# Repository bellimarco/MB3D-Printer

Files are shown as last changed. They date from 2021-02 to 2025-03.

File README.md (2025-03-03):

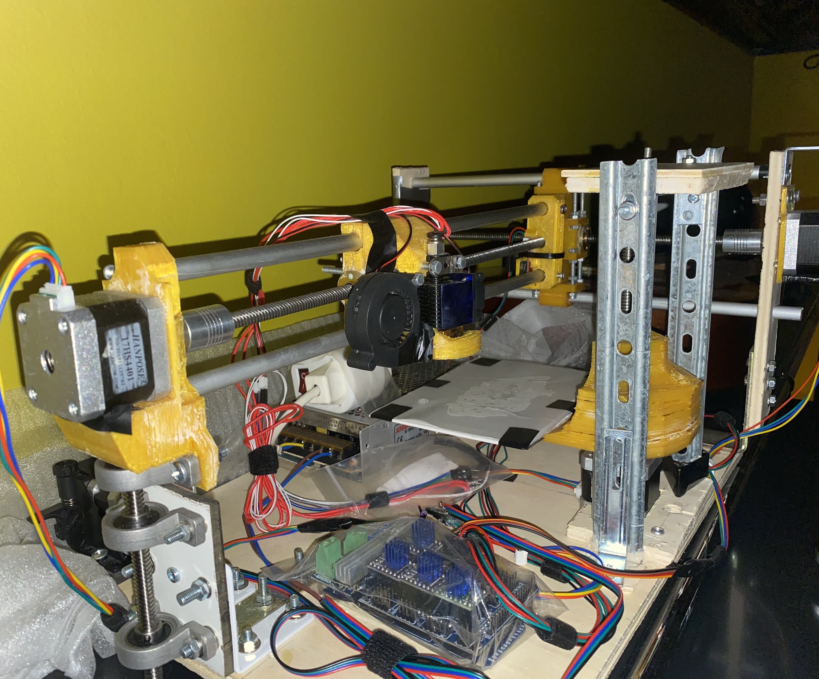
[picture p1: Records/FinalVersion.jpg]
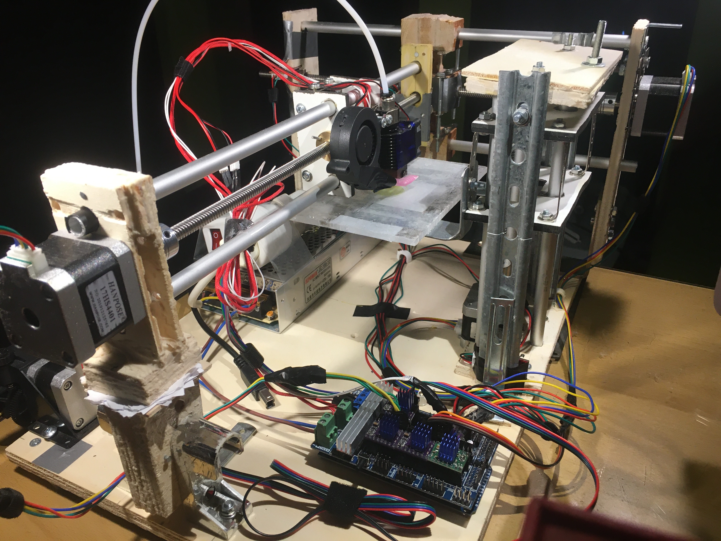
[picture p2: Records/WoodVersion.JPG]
 

The 3D Printer I built during the 2020 quarantine. Like the [plotter project](https://github.com/bellimarco/DisegnatoreRemoto) I had just finished, it is based on a polar setup with two stepper motors for radius and angle, and another stepper for the bed height.

An Arduino Mega with the RAMPS shield controls the actuators, filament extruder, end stops, heat block and thermistors; it receives Gcodes via serial from a computer. The bottleneck in printing speed was the microcontroller frequency, which wasn't enough to handle both serial communication and a smooth stepper motor control (which requires constantly sending precisely timed step signals to the four steppers). Therefore, I decided to separated these two processes: the Arduino listens on the serial port until filling a buffer of about 50 Gcodes, and then it starts executing them until the buffer is empty. The occasional waiting time (+-1 sec) for the Gcode buffer to fill up results inevitably in some artifacts on the final print due to the stillness of the printhead.

To create the Gcodes from the stl files I used the Cura software. With a NodeJS program, I translated the Cura files (meant for a classic CoreXY design) to a custom Gcode standard created to fit the model of my 3D printer. Then, I create a local server on the computer with another NodeJS program (mb3d.js) which sends via serial the Gcodes to the Arduino. The printing process can be monitored by a rudimentary user interface on a webpage connecting to the server.

In addition, the printer was built from scratch using wood and metal parts from my local carpentry shop. Only after having built a functioning wooden prototype, could I upgrade it with better 3D printed parts. I wanted to avoid building my first 3D printer with 3D printed parts obtained somewhere else because that feels a bit like cheating, doesn't it ?

## Resources
For more images and videos of the project I refer to my [Google Drive folder](https://drive.google.com/drive/folders/1L6Rk5TGIUBfg1ZFhCpQsbyhUCCYRQrp4?usp=share_link).

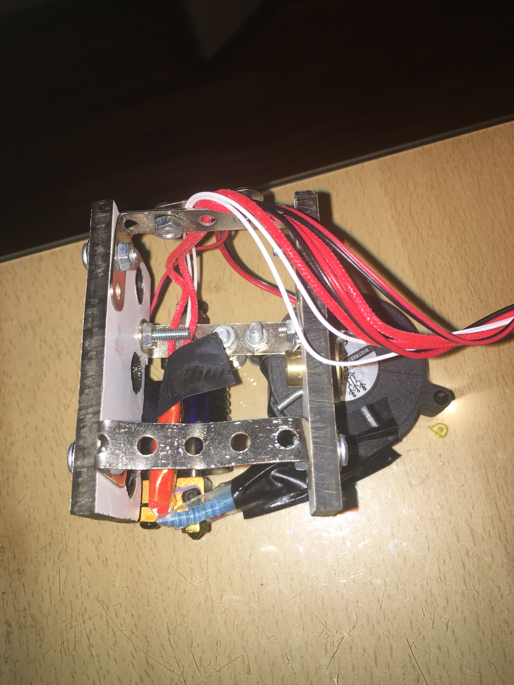
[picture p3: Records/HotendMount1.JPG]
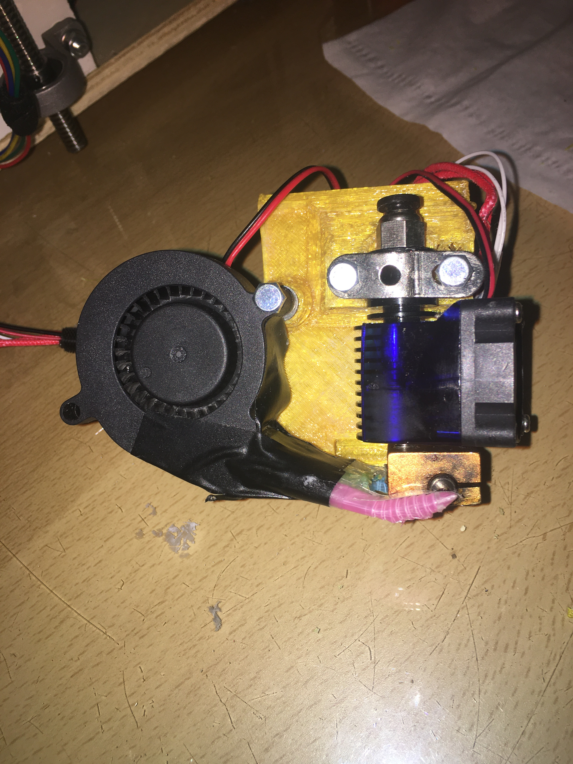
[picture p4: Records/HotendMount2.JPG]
 

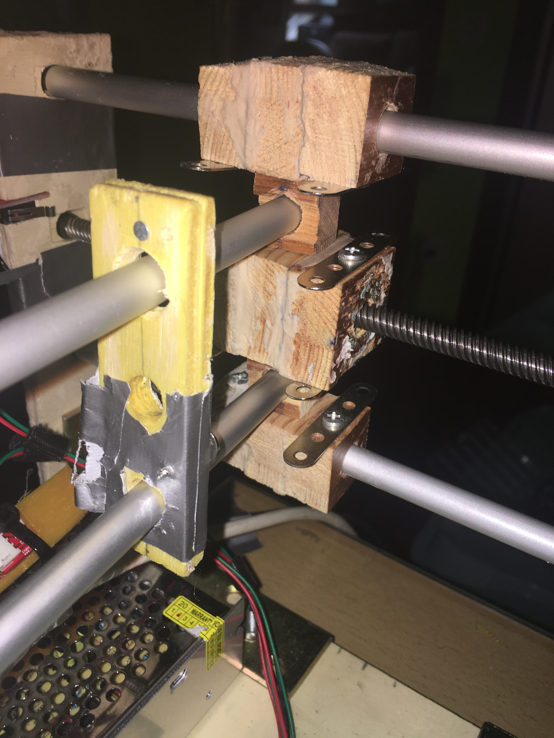
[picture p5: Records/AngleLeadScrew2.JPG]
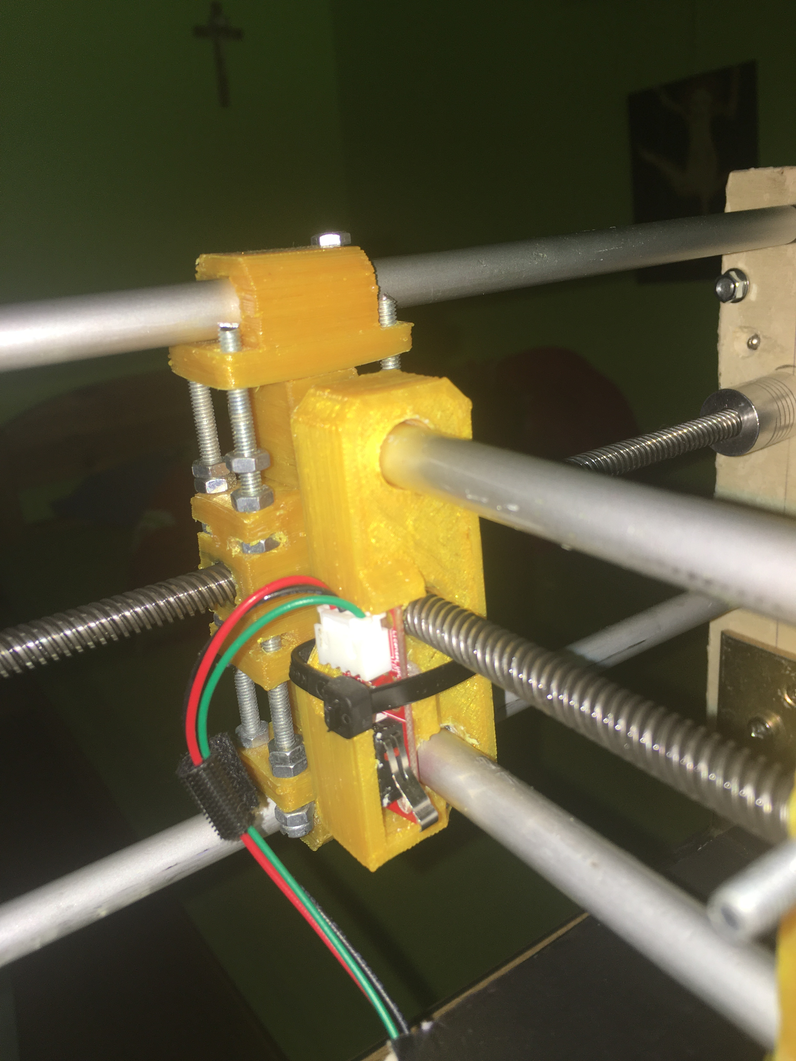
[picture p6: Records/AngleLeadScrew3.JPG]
 

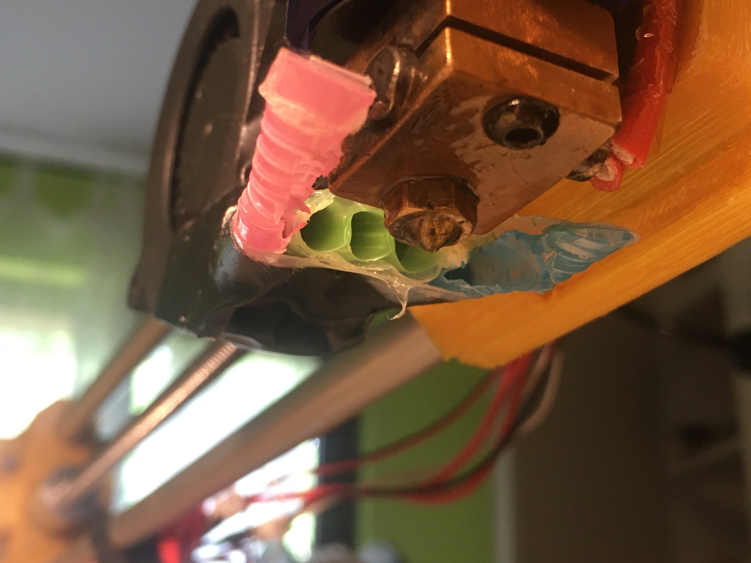
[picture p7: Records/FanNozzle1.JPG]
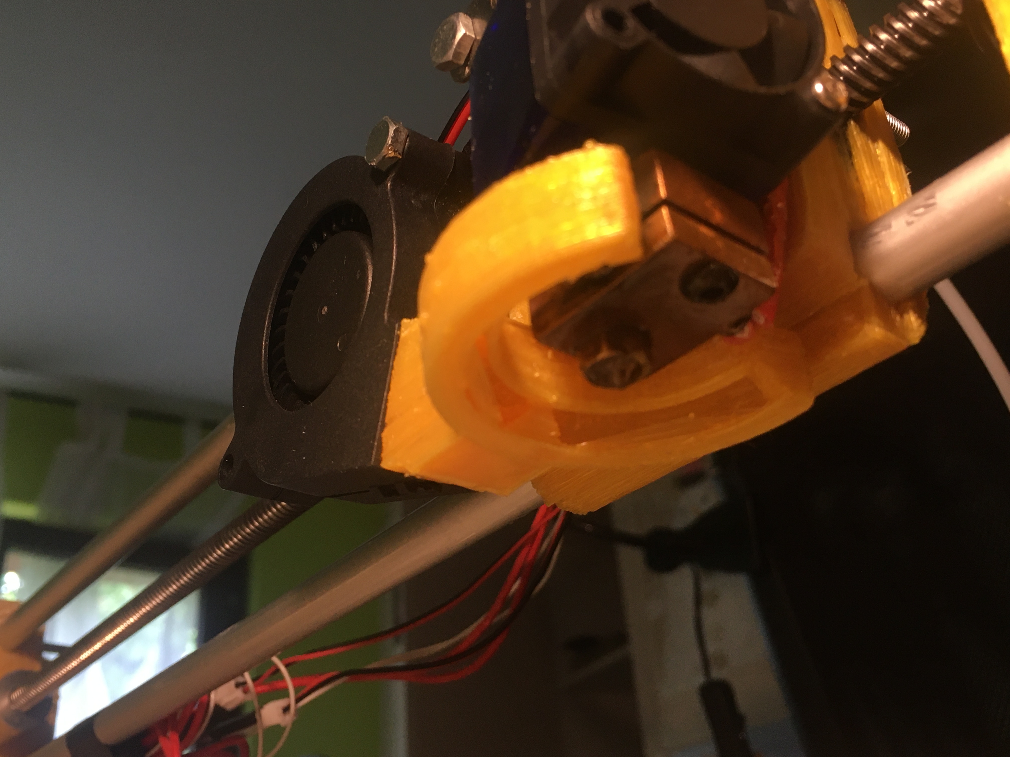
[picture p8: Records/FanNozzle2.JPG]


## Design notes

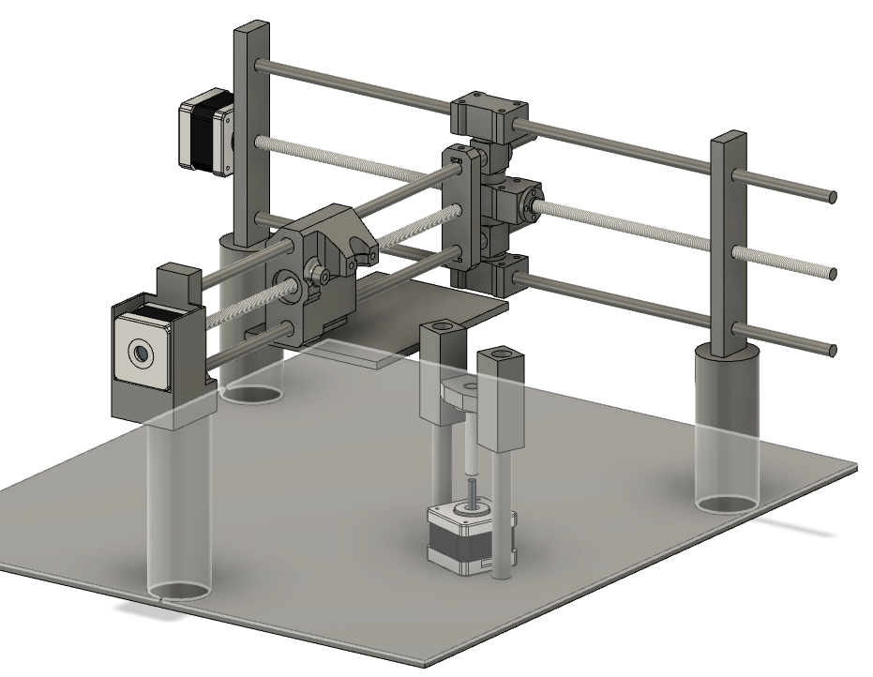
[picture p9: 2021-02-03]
Records/3dmodel.png

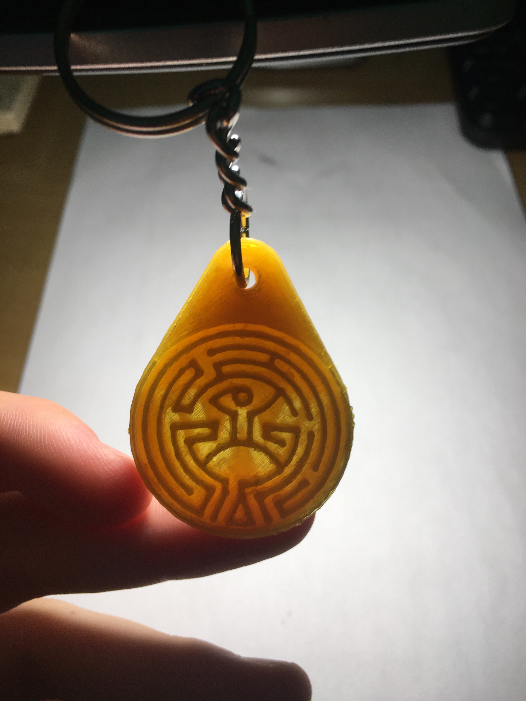
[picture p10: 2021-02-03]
Records/WestworldMaze2.JPG

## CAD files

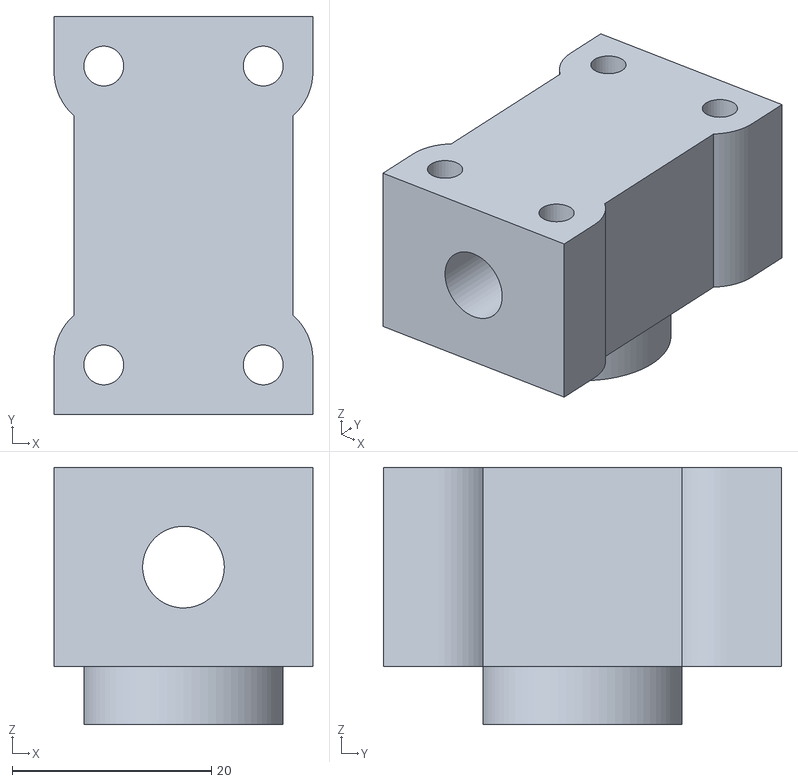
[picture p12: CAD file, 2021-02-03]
3DParts/ARailBott.stl
26.0 x 40.0 x 25.8

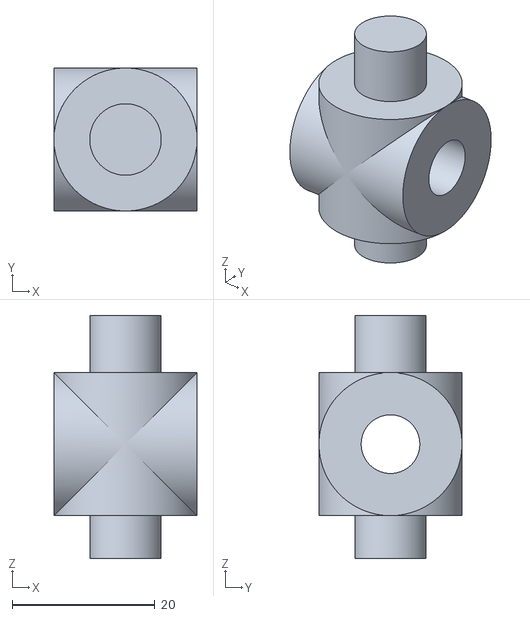
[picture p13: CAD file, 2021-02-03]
3DParts/RShaftSupportTop.stl
20.0 x 20.0 x 34.0

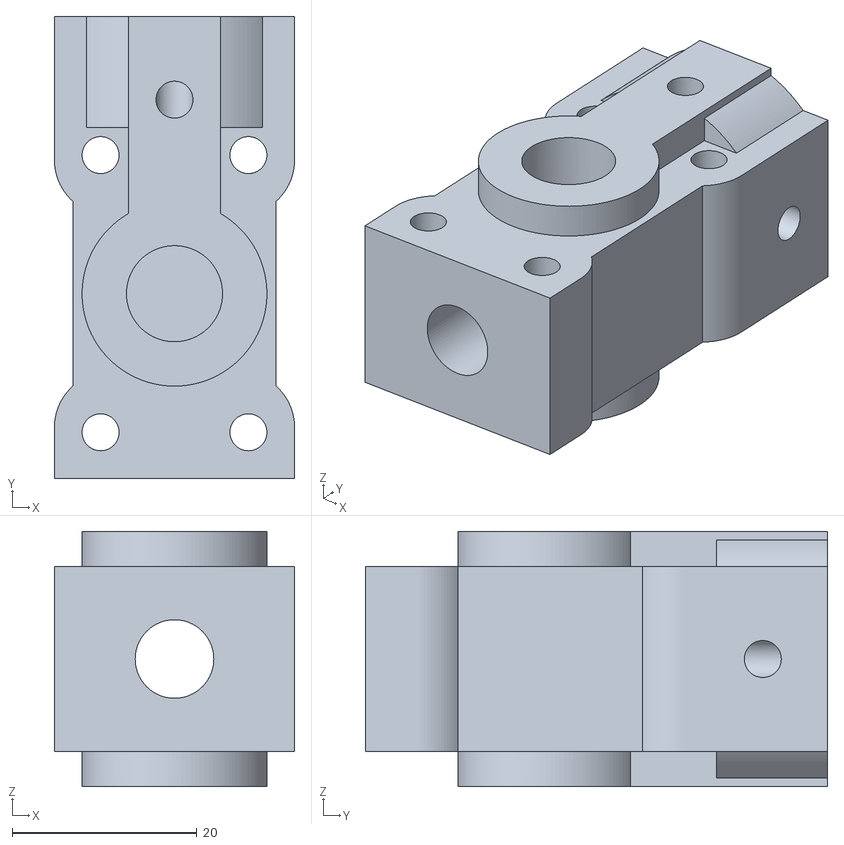
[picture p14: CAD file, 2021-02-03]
3DParts/ARailMiddle.stl
26.0 x 50.0 x 27.6

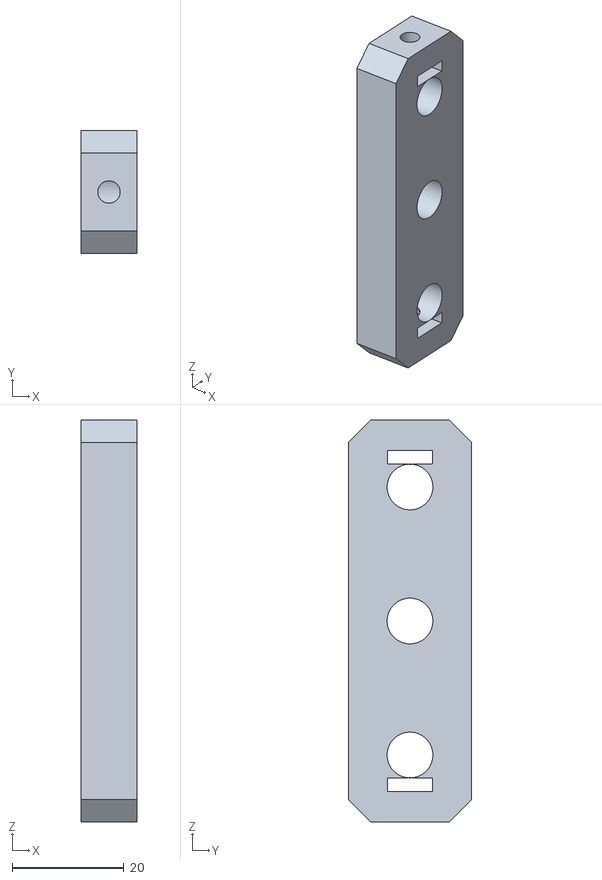
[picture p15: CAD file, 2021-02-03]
3DParts/LeadScrewRHolder.stl
10.0 x 22.0 x 72.0

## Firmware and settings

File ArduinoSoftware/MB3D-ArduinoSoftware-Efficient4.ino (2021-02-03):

#include "Pin.h"
#include "GlobalVariables.h"

#include <digitalWriteFast.h>

#include "ThermistorData.h"
#include "ThermalManagement.h"



//-----------------------------SETUP AND LOOP--------------------------

void setup() {

  Serial.begin(115200);
  SerialMsg.reserve(100);
  for(int i=0; i<BufferSize; i++){ Buffer[i]="/"; }

  SetPins();
  ResetPins();
 
}



void loop() {
  Time=millis();

  if(AutoNextCode){
    if(NextCodeTimert<Time){
      NextCodeTimert=Time+NextCodeTimerT;
      if(BufferHead!=BufferTail){
        AutoNextCode=false;
        Serial.print("autonext}");
        NextCode();
      }
    }
  }

  ThermalTimerUpdate();

  if(FinishedCode){
    CheckSerial();
    if(MotionCode && !NextPresent){
      RunMotionQueue();
    }
    FinishCode();
  }
  
  
  delay(LoopDelay);
}

//-----------------------------SETUP AND LOOP--------------------------





//---------------------COMMUNICATION ALGORITHM--------------------------

void serialEvent(){
  delay(100);
  CheckSerial();
}
void CheckSerial(){
  Time=millis();
  NextCodeTimert=Time+NextCodeTimerT;
  char c=' ';
  while(Serial.available()){
    c=Serial.read();
    if(c=='{'){
      SerialComplete=false;
      SerialMsg="";
    }else if(c=='}'){
      if(!SerialComplete){
        if(SerialMsg.equals("report")){
          PrintReport();
        }else{
          if(DepthLog){ Serial.print("echo/adding buffer: "+SerialMsg+"}"); }
          Serial.print("buf}");
          Buffer[BufferTail]=SerialMsg;
          BufferTail=(BufferTail+1==BufferSize)?0:(BufferTail+1);
        }
      }
      SerialComplete=true;
      SerialMsg="";
    }else if(!SerialComplete){
      SerialMsg+=c;
    }
  }
}

//finish the current code
void FinishCode(){
  MotionCode=false;
  FinishedCode=false;
  Serial.print("fin}");
  Buffer[BufferHead]="/";
  BufferHead=(BufferHead+1==BufferSize)?0:(BufferHead+1);
  if(BufferHead!=BufferTail){
    NextCode();
  }else{
    AutoNextCode=true;
    NextCodeTimert=0;
  }
}
//call next code in the buffer
void NextCode(){
  if(DepthLog){ Serial.print("echo/executing code: "+Buffer[BufferHead]+"}"); }
  GcodeCall(Buffer[BufferHead]);
}
//prints various information about the printer state
void PrintReport(){
  Serial.print("echo/report: ------------------------\n");
  Serial.print("buffer: ");
  for(int i=0; i<BufferSize; i++){
    if(i==BufferHead){Serial.print("H:");}
    if(i==BufferTail){Serial.print("T:");}
    Serial.print(String(Buffer[i])+"  ");
  }
  Serial.print("end of report ----------------------}");
}

//---------------------COMMUNICATION ALGORITHM--------------------------







//-----------------MOTOR COMANDS---------------------
void TurnOffMotors(){
  if(Ractive){ Ractive=false; Ron=false; digitalWrite(REnablePin,HIGH); digitalWrite(ROnPin,LOW); }
  if(Aactive){ Aactive=false; Aon=false; digitalWrite(AEnablePin,HIGH); digitalWrite(AOnPin,LOW); }
  if(Zactive){ Zactive=false; Zon=false; digitalWrite(ZEnablePin,HIGH); digitalWrite(ZOnPin,LOW); }
  if(Eactive){ Eactive=false; Eon=false; digitalWrite(EEnablePin,HIGH); digitalWrite(EOnPin,LOW); }
}
void TurnOnMotors(){
  if(Ractive){ Ron=true; digitalWrite(REnablePin,LOW); digitalWrite(ROnPin,HIGH); }
  if(Aactive){ Aon=true; digitalWrite(AEnablePin,LOW); digitalWrite(AOnPin,HIGH); }
  if(Zactive){ Zon=true; digitalWrite(ZEnablePin,LOW); digitalWrite(ZOnPin,HIGH); }
  if(Eactive){ Eon=true; digitalWrite(EEnablePin,LOW); digitalWrite(EOnPin,HIGH); }
}

//cartesian to step conversion
int CartToR=0; int CartToA=0;
void UpdateCartToRA(float x, float y){
  float a2=(y+NozzleToR)/(PivotX-x);
  float r1=sqrt(sq(PivotX-x)+y*(y+NozzleToR+NozzleToR));
  float a1=PivotToTangent*(a2*r1-NozzleToR)/(r1+a2*NozzleToR);
  CartToR=int((PivotX-r1)*RStepsPerMM*RMicrostep);
  CartToA=int(a1*AStepsPerMM*AMicrostep);
  //CartToR=int(x*CartToStepK);
  //CartToA=int(y*CartToStepK);
}
word CartToZ(float z){ return (word(max(0,z*ZStepsPerMM*ZMicrostep))); }
float CartToE(float e){ return e*EStepsPerMM*EMicrostep; }
//step to cartesian conversion
float StepToX=0; float StepToY=0;
void UpdateStepToXY(int r, int a){
  float r1=(PivotX-r/(RStepsPerMM*RMicrostep)); float a1=a/(AStepsPerMM*AMicrostep);
  float r2=sqrt(sq(NozzleToR)+sq(r1)); float a2=(a1+PivotToTangent*NozzleToR/r1)/(1-a1*NozzleToR/(PivotToTangent*r1));
  float c=sqrt(sq(PivotToTangent)+sq(a2));
  StepToX=r2*PivotToTangent/c-PivotX;
  StepToY=r2*a2/c-NozzleToR;
}
float StepToZ(word z){
  return float(z)/(ZStepsPerMM*ZMicrostep);
}
float StepToE(float e){
  return e/(EStepsPerMM*EMicrostep);
}


void FindEndstop(int n){
  if(DepthLog){
    Serial.print("echo/Searching endstop "+String(n)+"}");
  }
  int dt=int(500000.0/(StandardFeedRate/60*CartToStepK));
  boolean toggle=false;
  int stp=-1;
  int endstp=-1;
  switch (n){
    case 1: Ractive=true; digitalWrite(RDirPin,LOW); Rdir=false; stp=RStepPin; endstp=REndstopPin; RStep=REndstopPosition; RtargStep=RStep; break;
    case 2: Aactive=true; digitalWrite(ADirPin,LOW); Adir=false; stp=AStepPin; endstp=AEndstopPin; AStep=AEndstopPosition; AtargStep=AStep; break;
    case 3: Zactive=true; digitalWrite(ZDirPin,HIGH); Zdir=true; stp=ZStepPin; endstp=ZEndstopPin; ZStep=ZEndstopPosition; ZtargStep=ZStep; break;
  }
  TurnOnMotors();
  while(digitalRead(endstp)){
    toggle=!toggle; digitalWrite(stp,toggle);
    delayMicroseconds(dt);
  }
  TurnOffMotors();
  
  UpdateStepToXY(RStep,AStep);
  XCart=StepToX; YCart=StepToY;
  ZCart=StepToZ(ZStep); ECart=StepToE(EStep);
  XtargCart=XCart; YtargCart=YCart; ZtargCart=ZCart; EtargCart=ECart;
}



//-----------------MOTOR COMANDS---------------------








//----------------------MOTION PROFILE-----------------------------

//Motion Profile object
class MotionProfile{
  word dR=0; word dA=0; word dZ=0; word dE=0;
  boolean rdir=true; boolean adir=true; boolean zdir=true; boolean edir=true;
  //variables to calculate
  unsigned long dRSimstart=0UL; unsigned long dASimstart=0UL; unsigned long dESimstart=0UL; unsigned long dZSimstart=0UL;
  word ddRSim=0UL; word ddASim=0UL; word ddESim=0UL; //velocity change over dVT time, overflow warning
  unsigned long MotionT=0UL; //micros
  unsigned long ddVT1=0UL; unsigned long ddVT2=0UL; //micros
    
  public:
    MotionProfile(){
    }

    void MotionSetup(float Vtarg, float Vstart, float Vend,
        word dr, word da, word dz, word de, boolean rd, boolean ad, boolean zd, boolean ed){

      rdir=rd; adir=ad; zdir=zd; edir=ed;
      dR=dr; dA=da; dZ=dz; dE=de;

      float StepRatioR=0; float StepRatioA=0; float StepRatioE=0;
      
      float phase1_t=0; float phase1_2AS=0;
      float phase2_t=0; float phase2_2AS=0;
      float phase3_t=0; float phase3_2AS=0;
      float Mot2AS=2*AccelStep*dStep;
      float T=0;
      if(dR!=0 ||dA!=0){
        StepRatioR=dR/dStep; StepRatioA=dA/dStep; StepRatioE=dE/dStep;
        
        float V1=min(Vstart,Vend);
        float V2=max(Vstart,Vend);
        phase1_t=(V2-V1)/AccelStep;
        phase1_2AS=sq(V2)-sq(V1);
        //if can't accelerate in time to V2
        if(Mot2AS<phase1_2AS){
          phase1_2AS=Mot2AS;
          phase1_t=((Vend<Vstart)?-1:1)*(sqrt(sq(Vstart)+((Vend<Vstart)?-1:1)*phase1_2AS)-Vstart)/AccelStep;
          T=phase1_t;
        }else{
          phase2_t=(Vtarg-V2)/AccelStep;
          phase2_2AS=2*(sq(Vtarg)-sq(V2));
          //if can't accelerate in time to Vtarg
          if(Mot2AS-phase1_2AS<phase2_2AS){
            phase2_2AS=Mot2AS-phase1_2AS;
            phase2_t=(sqrt(sq(V2)+phase2_2AS/2)-V2)/AccelStep;
            T=phase1_t+2*phase2_t;
          }else{
            phase3_2AS=Mot2AS-phase1_2AS-phase2_2AS;
            phase3_t=phase3_2AS/(AccelStep*4*Vtarg);
            T=phase1_t+2*phase2_t+2*phase3_t;
          }
        }
        
        //velocity change over dVT time during accel/decel
        ddRSim=StepRatioR*ddSimStandard+1; ddASim=StepRatioA*ddSimStandard+1; ddESim=StepRatioE*ddSimStandard+1;
         
        //position change over GoSimT time at start
        dRSimstart=Vstart*StepRatioR*dSimStandard+0.5*ddRSim+0.5; dASimstart=Vstart*StepRatioA*dSimStandard+0.5*ddASim+0.5; dESimstart=Vstart*StepRatioE*dSimStandard+0.5*ddESim+0.5; dZSimstart=dZ/T*dSimStandard+1;
        
        if(Vend>=Vstart){ ddVT1=((phase1_t+phase2_t)*1000000); ddVT2=((phase1_t+phase2_t+2*phase3_t)*1000000); }
        else{ ddVT1=(phase2_t*1000000); ddVT2=((phase2_t+2*phase3_t)*1000000); }
        
      }else{
        dRSimstart=0UL; dASimstart=0UL;
        ddRSim=0; ddASim=0; ddESim=0;
        ddVT1=0UL; ddVT2=0UL; 
        
        //Z > E motion profile priority
        if(dZ!=0){
          dZSimstart=Vtarg*VtargToVZDefaultK*dSimStandard+1;
          T=dZ/(Vtarg*VtargToVZDefaultK);
          dESimstart=dE/T*dSimStandard+1;
        }
        else if(dE!=0){
          dESimstart=Vtarg*CartToExtrK*dSimStandard+1;
          T=dE/(Vtarg*CartToExtrK);
        }
        
      }
      MotionT=T*1000000;

      if(DepthLog){
        Serial.print("echo/calculated motion profile, d: "+String(dR)+", "+String(dA)+", "+String(dZ)+", "+String(dE)+"\n"
        +"Vstart: "+String(Vstart)+", Vtarg: "+String(Vtarg)+", Vend: "+String(Vend)+"\n");
        if(DepthLogPlus){
          Serial.print("dStep: "+String(dStep)+", phase S: "+String(phase1_2AS/(2*AccelStep))+", "+String(phase2_2AS/(2*AccelStep))+", "+String(phase3_2AS/(2*AccelStep))+"\n"
          +"MotionT: "+String(MotionT)+", phase t: "+String(phase1_t)+", "+String(phase2_t)+", "+String(phase3_t));
        }else{
          Serial.print("MotionT: "+String(MotionT));
        }
        Serial.print("\ndSimstart: "+String(dRSimstart)+", "+String(dASimstart)+", "+String(dZSimstart)+", "+String(dESimstart)+"\n"
        +"ddSim: "+String(ddRSim)+", "+String(ddASim)+", "+String(ddESim)+"}");
      }
    }
    //prepare the relevant motors before runmotionqueue really begins
    void Prepare(){
      if(dR!=0){Ractive=true;}
      if(dA!=0){Aactive=true;}
      if(dZ!=0){Zactive=true;}
      if(dE!=0){Eactive=true;}
    }

    void PrintPhaseLog(){
      Serial.print("echo/T: "+String(Tstate)+", GoSimt: "+String(GoSimt)+", phase "+String(MotionPhase));
      if(DepthLogPlus){
        Serial.print("\nd: "+String(dR)+", "+String(dA)+", "+String(dZ)+", "+String(dE)+"\n"
        +"dSim: "+String(dRSim)+", "+String(dASim)+", "+String(dZSim)+", "+String(dESim)+"\n"
        +"Sim: "+String(RSim)+", "+String(ASim)+", "+String(ZSim)+", "+String(ESim));
      }
      Serial.print("}");
    }
    
    void GoTarget(){
      MotionPhase=4;
      if(dR!=0){ dRSim=dRSimstart; RSim=0UL; if(rdir){digitalWriteFast(RDirPin,HIGH);}else{digitalWriteFast(RDirPin,LOW);} MotionPhase=1; }
      if(dA!=0){ dASim=dASimstart; ASim=0UL; if(adir){digitalWriteFast(ADirPin,HIGH);}else{digitalWriteFast(ADirPin,LOW);} MotionPhase=1; }
      if(dZ!=0){ dZSim=dZSimstart; ZSim=0UL; if(zdir){digitalWriteFast(ZDirPin,HIGH);}else{digitalWriteFast(ZDirPin,LOW);}}
      if(dE!=0){ dESim=dESimstart; ESim=0UL; if(edir){digitalWriteFast(EDirPin,HIGH);}else{digitalWriteFast(EDirPin,LOW);}}

      if(DepthLog){
        /*Serial.print("echo/starting motion, MotionT: "+String(MotionT)+", phase "+String(MotionPhase)+"\n"
        +"ddVT1: "+String(ddVT1)+", ddVT2: "+String(ddVT2));
        if(DepthLogPlus){
          Serial.print("\nd: "+String(dR)+", "+String(dA)+", "+String(dZ)+", "+String(dE)+"\n"
          +"dSim: "+String(dRSim)+", "+String(dASim)+", "+String(dZSim)+", "+String(dESim)+"\n"
          +"Sim: "+String(RSim)+", "+String(ASim)+", "+String(ZSim)+", "+String(ESim));
        }
        Serial.print("}");*/
        Serial.print("echo/starting motion, MotionT: "+String(MotionT)+", phase "+String(MotionPhase)
        +"\nd: "+String(dR)+", "+String(dA)+", "+String(dZ)+", "+String(dE)+"}");
      }

      Go=true;
      while(Go){
        Tstate=micros()-Tstart;
        if(Tstate>GoSimt){
          Go=false;
          GoSimt+=GoSimT;

          if(Tstate>dVt){
            dVt+=dVT;
            if(Tstate>MotionT){
              MotionPhase=4; if(DepthLog){PrintPhaseLog();}
              dVt=1000000000UL;
            }else if(Tstate>ddVT2){
              if(MotionPhase==2){ MotionPhase=3; if(DepthLog){PrintPhaseLog();} }
              dRSim-=ddRSim; dASim-=ddASim; dESim-=ddESim;
            }else if(Tstate<ddVT1){
              dRSim+=ddRSim; dASim+=ddASim; dESim+=ddESim;
            }else if(MotionPhase==1){
              MotionPhase=2; if(DepthLog){PrintPhaseLog();}
            }
          }
          
          if(dR!=0){ Go=true; RSim+=dRSim;
            if(RSim>GoSimScale){ digitalWriteFast(RStepPin,HIGH); RSim-=GoSimScale; dR--; delayMicroseconds(5); digitalWriteFast(RStepPin,LOW); }
          }
          if(dA!=0){ Go=true; ASim+=dASim;
            if(ASim>GoSimScale){ digitalWriteFast(AStepPin,HIGH); ASim-=GoSimScale; dA--; delayMicroseconds(5); digitalWriteFast(AStepPin,LOW); }
          }
          if(dZ!=0){ Go=true; ZSim+=dZSim;
            if(ZSim>GoSimScale){ digitalWriteFast(ZStepPin,HIGH); ZSim-=GoSimScale; dZ--; delayMicroseconds(5); digitalWriteFast(ZStepPin,LOW); }
          }
          if(dE!=0){ Go=true; ESim+=dESim;
            if(ESim>GoSimScale){ digitalWriteFast(EStepPin,HIGH); ESim-=GoSimScale; dE--; delayMicroseconds(5); digitalWriteFast(EStepPin,LOW); }
          }
        }
        if(Go){delayMicroseconds(GoT);}
      }
      Tstart=micros();
      dVt=0UL+dVT; GoSimt=0UL; MotionPhase=5;
      //PrintPhaseLog();
      if(DepthLog){
        Serial.print("echo/T: "+String(Tstate)+", MotionT: "+String(MotionT)
          +"\ndSim: "+String(dRSim)+", "+String(dASim)+", "+String(dZSim)+", "+String(dESim)+"}");
      }
    }
};

MotionProfile MotionBuffer[MotionBufferSize];



void QueueMotionProfile(){
  if(!NextPresent){
    UpdateCartToRA(XtargCart,YtargCart);
    RtargStep=CartToR;
    AtargStep=CartToA;
    ZtargStep=CartToZ(ZtargCart);
    EtargStep=CartToE(EtargCart);
    vtarg=FeedRate/60*CartToStepK;
    vstart=0;
  }else{
    RtargStep=RnexttargStep;
    AtargStep=AnexttargStep;
    ZtargStep=CartToZ(ZtargCart);
    EtargStep=CartToE(EtargCart);
    vtarg=vnxttarg;
    vstart=QueueProfileLastVend;
  }
  XnexttargCart=XtargCart; YnexttargCart=YtargCart;
  RnexttargStep=RtargStep; AnexttargStep=AtargStep;
  dr=word(abs(long(RtargStep)-long(RStep))); da=word(abs(long(AtargStep)-long(AStep)));
  dz=word(abs(long(ZtargStep)-long(ZStep))); de=word(min(65536,abs(EtargStep-EStep)));
  if(NextPresent){ dStep=dnextStep; }
  else{ dStep=sqrt(sq(float(dr))+sq(float(da))); }

  byte i=(BufferHead+1==BufferSize)?0:(BufferHead+1);
  if(i!=BufferTail && Buffer[i][0]=='G'
      && (Buffer[i][1]=='1' || Buffer[i][1]=='0')
      && (MotionBufferFilled+1<MotionBufferSize)){
    NextPresent=true;

    float attr=GcodeParser(Buffer[i],'F');
    if(attr!=987654321){ vnxttarg=attr/60*CartToStepK; }else{vnxttarg=vtarg;}
      
    attr=GcodeParser(Buffer[i],'X');
    if(attr!=987654321){ if(AbsolutePositioning){ XnexttargCart=attr; }else{ XnexttargCart+=attr; }}
    attr=GcodeParser(Buffer[i],'Y');
    if(attr!=987654321){ if(AbsolutePositioning){ YnexttargCart=attr; }else{ YnexttargCart+=attr; }}
    
    if(XnexttargCart!=XtargCart||YnexttargCart!=YtargCart){ 
      UpdateCartToRA(XnexttargCart,YnexttargCart);
      RnexttargStep=CartToR; AnexttargStep=CartToA;
      dnextStep=sqrt(sq(float(RnexttargStep)-float(RtargStep))+sq(float(AnexttargStep)-float(AtargStep)));
      if(dStep!=0){
        vend=min(sqrt(2*AccelStep*dnextStep),min(vtarg,vnxttarg*sq(sq(sq(max(0,
          ((float(RtargStep)-float(RStep))*(float(RnexttargStep)-float(RtargStep))+(float(AtargStep)-float(AStep))*(float(AnexttargStep)-float(AtargStep)))/
          (dStep*dnextStep)))))));
      }else{
        vend=0;
      }
    }else{
      vend=0;
      dnextStep=0;
    }
  }else{
    NextPresent=false;
    vnxttarg=vtarg; vend=0;
    dnextStep=0;
  }
  
  QueueProfileLastVend=vend;
  vend=max(MinVend,vend);
  MotionBuffer[MotionBufferFilled].MotionSetup(vtarg,vstart,vend, dr,da,dz,de,(RtargStep>=RStep),(AtargStep>=AStep),(ZtargStep>=ZStep),(EtargStep>=EStep));
  MotionBufferFilled++;

  XCart=XtargCart; YCart=YtargCart;
  ZCart=ZtargCart; ECart=EtargCart;
  RStep=RtargStep; AStep=AtargStep;
  ZStep=ZtargStep; EStep=EtargStep;

  FinishedCode=true;
}

void RunMotionQueue(){
  if(ThermalOn && HotendHeaterOn){
    analogWrite(HotendHeaterPin,byte(HotendPDIdealEffort*255+0.45));
  }
  for(byte i=0; i<MotionBufferFilled; i++){
    MotionBuffer[i].Prepare();
  }
  TurnOnMotors();
  Serial.print("run}");
  Tstart=micros();
  for(byte i=0; i<MotionBufferFilled; i++){
    MotionBuffer[i].GoTarget();
  }
  Serial.print("endrun}");
  TurnOffMotors();
  MotionBufferFilled=0;
}



//----------------------MOTION PROFILE-----------------------------






//-----------------GCODE INTERPRETING AND EXECUTION---------------------

//given a Gcode and a char attribute, return the value or the error code
float GcodeParser(String str, char a){
  String val="";
  int n=str.indexOf(a);
  if(n!=-1){
    while((str[n+1]-'0'>=0 && str[n+1]-'0'<=9) || str[n+1]=='-' || str[n+1]=='.'){
      val+=str[n+1];
      n++;
    }
    return val.toFloat();
  }else{
    return 987654321;
  }
}

//given a Gcode, updates the variables modified by the attributes and calls the comand
void GcodeCall(String str){
  int code=-1;
  if(str[0]=='C'){
    //update the possible attributes of the G codes
    float attr=0;
    attr=GcodeParser(str,'X');
    if(attr!=987654321){ C=attr; }
    
    code=GcodeParser(str,'C');
    switch(code){
      case 0:C0();break;
      case 1:C1();break;
      case 2:C2();break;
      default:unknown(str);break;
    }
  }else if(str[0]=='G'){
    //update the possible attributes of the G codes
    X=GcodeParser(str,'X');
    Y=GcodeParser(str,'Y');
    Z=GcodeParser(str,'Z');
    E=GcodeParser(str,'E');
    F=GcodeParser(str,'F');
    
    code=GcodeParser(str,'G');
    switch(code){
      case 0:
      case 1:G1();break;
      case 28:G28();break;
      case 90:G90();break;
      case 91:G91();break;
      case 92:G92();break;
      default:unknown(str);break;
    }
  }else if(str[0]=='M'){
    //update the possible attributes of the M codes
    S=GcodeParser(str,'S');

    code=GcodeParser(str,'M');
    switch(code){
      case 83:M83();break;
      case 84:M84();break;
      case 104:M104();break;
      case 106:M106();break;
      case 107:M107();break;
      case 109:M109();break;
      case 140:M140();break;
      default:unknown(str);break;
    }
  }else if(str[0]=='T'){

    code=GcodeParser(str,'T');
    switch(code){
      case 0:T0();break;
      default:unknown(str);break;
    }
  }else{
    unknown(str);
  }
}
//if the software doesnt know
void unknown(String str){
  Serial.print("echo/received unknown Gcode: "+String(str)+"}");
  delay(4000);
  FinishedCode=true;
}  

//C codes, customized for mb3d software
void C0(){
  DepthLog=(C==1);
  FinishedCode=true;
}
void C1(){
  FindEndstop(C);
  FinishedCode=true;
}
void C2(){
  DepthLogPlus=(C==1);
  FinishedCode=true;
}


//G codes
void G0(){
  delay(5000);
  FinishedCode=true;
}
void G1(){
  MotionCode=true;
  if(F!=987654321){FeedRate=F;}
  if(X!=987654321){if(AbsolutePositioning){XtargCart=X;}else{XtargCart+=X;}}
  if(Y!=987654321){if(AbsolutePositioning){YtargCart=Y;}else{YtargCart+=Y;}}
  if(Z!=987654321){if(AbsolutePositioning){ZtargCart=Z;}else{ZtargCart+=Z;}}
  if(E!=987654321){if(AbsoluteExtrusion){EtargCart=E;}else{EtargCart+=E;}}
  
  QueueMotionProfile();
}
void G28(){ 
  boolean x=false; boolean y=false; boolean z=false;
  if(X!=987654321){x=true; }
  if(Y!=987654321){y=true; }
  if(Z!=987654321){z=true;}
  if(X==987654321 && Y==987654321 && Z==987654321){ x=true; y=true; z=true; }
  FeedRate=StandardFeedRate;
  if(DepthLog){ Serial.print("echo/started homing: "+String(x)+", "+String(y)+", "+String(z)+"}"); }

  UpdateCartToRA(XHome,YHome);
  int rhome=CartToR; int ahome=CartToA; word zhome=CartToZ(ZHome);

  if(x){FindEndstop(1); digitalWrite(RDirPin,HIGH); RtargStep=rhome; dr=word(abs(long(RtargStep)-long(RStep)));}else{dr=0;}
  Time=millis(); ThermalTimerUpdate();
  if(y){FindEndstop(2); digitalWrite(ADirPin,HIGH); AtargStep=ahome; da=word(abs(long(AtargStep)-long(AStep)));}else{da=0;}
  Time=millis(); ThermalTimerUpdate();
  if(z){FindEndstop(3); digitalWrite(ZDirPin,LOW);  ZtargStep=zhome; dz=word(abs(long(ZtargStep)-long(ZStep)));}else{dz=0;}
  Time=millis(); ThermalTimerUpdate();

  dr*=4; da*=4; //for temporary 2mm lead screw setup----------------------------------

  MotionProfile homing=MotionProfile();  
  homing.MotionSetup(FeedRate/60*CartToStepK,0,0,dr,da,dz,0,(rhome>=RStep),(ahome>=AStep),(zhome>=ZStep),true);
  homing.Prepare();
  TurnOnMotors(); delay(1);
  homing.GoTarget();
  TurnOffMotors();

  if(x){ RStep=rhome;}
  if(y){ AStep=ahome;} 
  if(z){ ZStep=zhome;}
  UpdateStepToXY(RStep,AStep);
  XCart=StepToX; YCart=StepToY;
  ZCart=StepToZ(ZStep);
  XtargCart=XCart; YtargCart=YCart; ZtargCart=ZCart; EtargCart=ECart;

  if(DepthLog){ Serial.print("echo/ended homing, "+String(XCart)+", "+String(YCart)+", "+String(ZCart)+"}"); }
  FinishedCode=true;
}
void G90(){ AbsolutePositioning=true; FinishedCode=true; }
void G91(){ AbsolutePositioning=false; FinishedCode=true; }
void G92(){
  if(X!=987654321){XCart=X;}
  if(Y!=987654321){YCart=Y;}
  if(Z!=987654321){ZCart=Z;}
  if(E!=987654321){ECart=E;}
  UpdateCartToRA(XCart,YCart);
  RStep=CartToR; AStep=CartToA;
  ZStep=CartToZ(ZCart); EStep=CartToE(ECart);

  FinishedCode=true;
}

//M codes
void M82(){ AbsoluteExtrusion=true; FinishedCode=true; }
void M83(){ AbsoluteExtrusion=false; FinishedCode=true; }
void M84(){ FinishedCode=true; }
void M104(){
  if(S!=987654321){ if(!ThermalOn){ToggleThermal();}HotendUpdateTempTarg(); }
  else{ ToggleThermal(); }
  FinishedCode=true;
}
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

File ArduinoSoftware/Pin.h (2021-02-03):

const byte RStepPin=54;
const byte RDirPin=55;
const byte REnablePin=38;
const byte REndstopPin=3;
const byte AStepPin=60;
const byte ADirPin=61;
const byte AEnablePin=56;
const byte AEndstopPin=2;
const byte ZStepPin=46;
const byte ZDirPin=48;
const byte ZEnablePin=62;
const byte ZEndstopPin=18;
const byte EStepPin=26;
const byte EDirPin=28;
const byte EEnablePin=24;
const byte E0StepPin=36;
const byte E0DirPin=34;
const byte E0EnablePin=30;

const byte HotendThermistorPin=67;
const byte HotendHeaterPin=8;
const byte HotendFanPin=10;
const byte PrintFanPin=9;

const byte ROnPin=17;
const byte AOnPin=23;
const byte ZOnPin=25;
const byte EOnPin=27;
const byte MotorOnGroundPin=16;


void SetPins(){
  pinMode(RStepPin,OUTPUT);
  pinMode(RDirPin,OUTPUT);
  pinMode(REnablePin,OUTPUT);
  pinMode(REndstopPin,INPUT);
  pinMode(AStepPin,OUTPUT);
  pinMode(ADirPin,OUTPUT);
  pinMode(AEnablePin,OUTPUT);
  pinMode(AEndstopPin,INPUT);
  pinMode(ZStepPin,OUTPUT);
  pinMode(ZDirPin,OUTPUT);
  pinMode(ZEnablePin,OUTPUT);
  pinMode(ZEndstopPin,INPUT);
  pinMode(EStepPin,OUTPUT);
  pinMode(EDirPin,OUTPUT);
  pinMode(EEnablePin,OUTPUT);

  pinMode(HotendThermistorPin,INPUT);
  pinMode(HotendHeaterPin,OUTPUT);
  pinMode(HotendFanPin,OUTPUT);
  pinMode(PrintFanPin,OUTPUT);

  pinMode(ROnPin,OUTPUT);
  pinMode(AOnPin,OUTPUT);
  pinMode(ZOnPin,OUTPUT);
  pinMode(EOnPin,OUTPUT);
  pinMode(MotorOnGroundPin,OUTPUT);
}
void ResetPins(){
  digitalWrite(RStepPin,LOW);
  digitalWrite(RDirPin,HIGH);
  digitalWrite(REnablePin,HIGH);
  digitalWrite(AStepPin,LOW);
  digitalWrite(ADirPin,HIGH);
  digitalWrite(AEnablePin,HIGH);
  digitalWrite(ZStepPin,LOW);
  digitalWrite(ZDirPin,HIGH);
  digitalWrite(ZEnablePin,HIGH);
  digitalWrite(EStepPin,LOW);
  digitalWrite(EDirPin,HIGH);
  digitalWrite(EEnablePin,HIGH);

  digitalWrite(HotendHeaterPin,LOW);
  digitalWrite(HotendFanPin,LOW);
  digitalWrite(PrintFanPin,LOW);

  digitalWrite(ROnPin,LOW);
  digitalWrite(AOnPin,LOW);
  digitalWrite(ZOnPin,LOW);
  digitalWrite(EOnPin,LOW);
  digitalWrite(MotorOnGroundPin,LOW);
}
